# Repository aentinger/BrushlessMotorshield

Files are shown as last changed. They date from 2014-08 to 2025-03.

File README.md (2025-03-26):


💾 Brushless Motorshield
========================



# 📸 Image

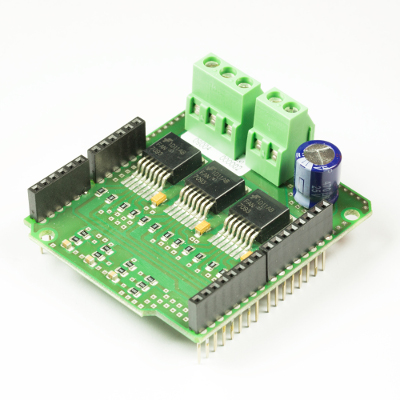
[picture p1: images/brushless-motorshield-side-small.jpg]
LXRobotics P3 BrushlessMotorshield


# 📂 Description

The Brushless Motorshield facilitates the control of a brushless motor with high performance (up to 46 A per phase). Furthermore so-called brushless gimbal motors can be controlled. For a quick and easy start, an open source Arduino library with sample programs is available.

**Features**

* Control of a brushless motor (BLDC Motor)
* Control of a Brushless Gimbal Motor
* Voltage supply range: 7.4 -14.8 V
* Can be used with 2S, 3S and 4S LiPo-battery
* High performance: Maximum continuous output current per phase: 46 A
* Motor drivers are protected against short circuit (to ground/supply), overheating, overvoltage and undervoltage
* Arduino Library with example programs is available on GitHub

# 🎥 [Video](images/brushless_motorshield_demo.mp4)

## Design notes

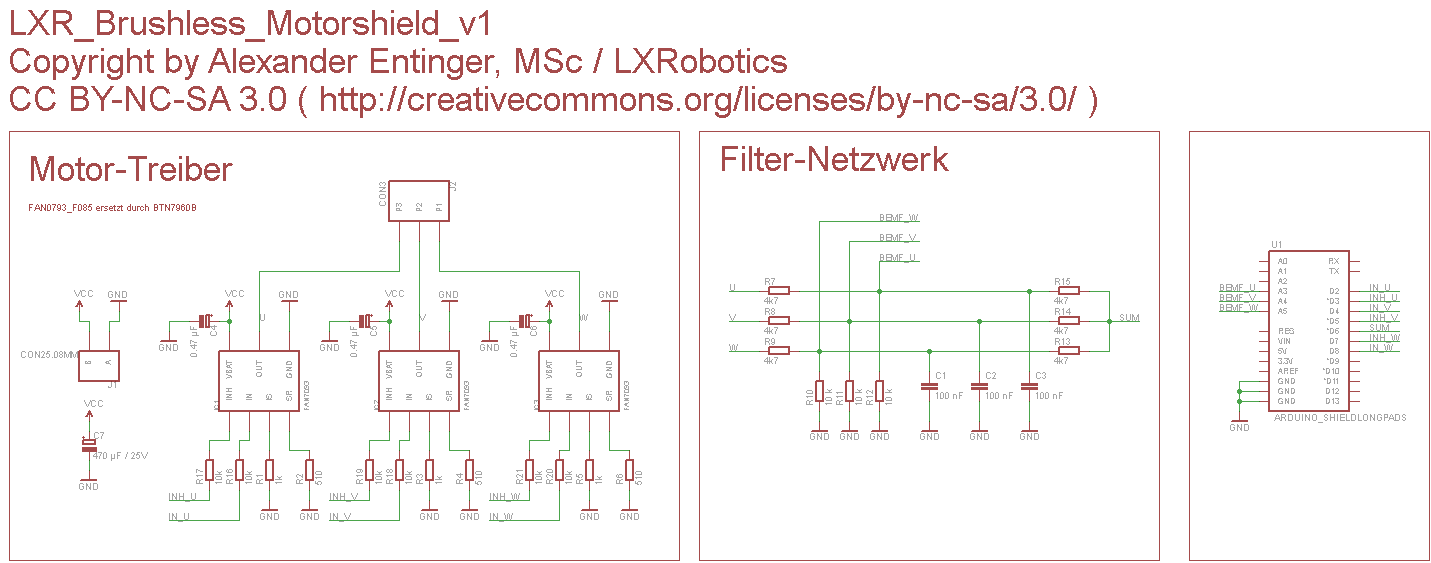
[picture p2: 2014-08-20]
hardware/lxr_brushless_motorshield_v1.png

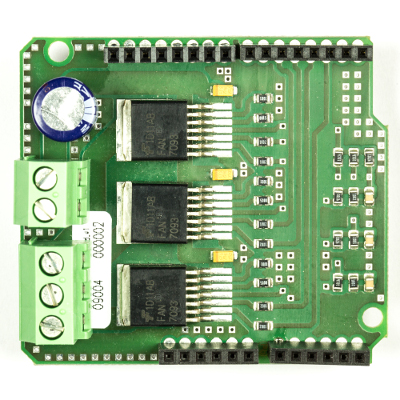
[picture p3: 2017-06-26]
images/brushless-motorshield-top-small.jpg

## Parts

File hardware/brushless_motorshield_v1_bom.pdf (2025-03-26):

Menge | Schaltplan | Bezeichnung | Farnell Bestell Nummer | Preis (1 Stück) | Gesamtpreis | Wird bestückt | Footprint | Säckchen | ESD
1 | J1 | Schraubklemme 2 Polig | 3041165 | € 1,12 | € 1,12 | | | S1
3 | IC1, IC2, IC3 | FAN7093 Leistungshalbbrücke | 2290282 | € | 6,99 | € | 20,97 | x | Bei Farnell aus dem Sortiment genommen, Ersatztyp ist BTN7960B, Digikey-Bauteil-Bezeichnung BTN7960BCT-ND
3 | C4, C5, C6 | KEMET Bauform A, 25 V, 470 nF, Tantal Ko | 1457425 | € 0,15 | € 0,46 | x
3 | C1, C2, C3 | 100 nF, 100 V, 0805, Keramikkondensator | 1759144 | € 0,01 | € 0,03 | x
1 | J2 | Schraubklemme 3 Polig | 3041177 | € 2,54 | € 2,54 | | S1
1 | C7 | 470 µF, 25 V, Elko, Radial | 1848502 | € 0,37 | € 0,37 | | S2 | x
9 | R10, R11, R12, R16, R17, R18, R19, R20, R21 | 10k, 0805, Widerstand SMD | 1469856 | € 0,02 | € 0,20 | x
3 | R1, R3, R5 | 1k, 0805, Widerstand SMD | 1469847 | € 0,02 | € 0,07 | x
3 | R2, R4, R6 | 510R, 0805, Widerstand SMD | 1653016 | € 0,10 | € 0,29 | x
6 | R7, R8, R9, R13, R14, R15 | 4k7, 0805, Widerstand SMD | 1469923 | € 0,02 | € 0,12 | x
1 | Satz Arduino Stiftleisten | ELV | € | 0,75 | € | 0,75 | - | http://www.elv.at/buchsenleisten-set-fuer-arduino-boards.html
| | | Summe | | € | 26,92

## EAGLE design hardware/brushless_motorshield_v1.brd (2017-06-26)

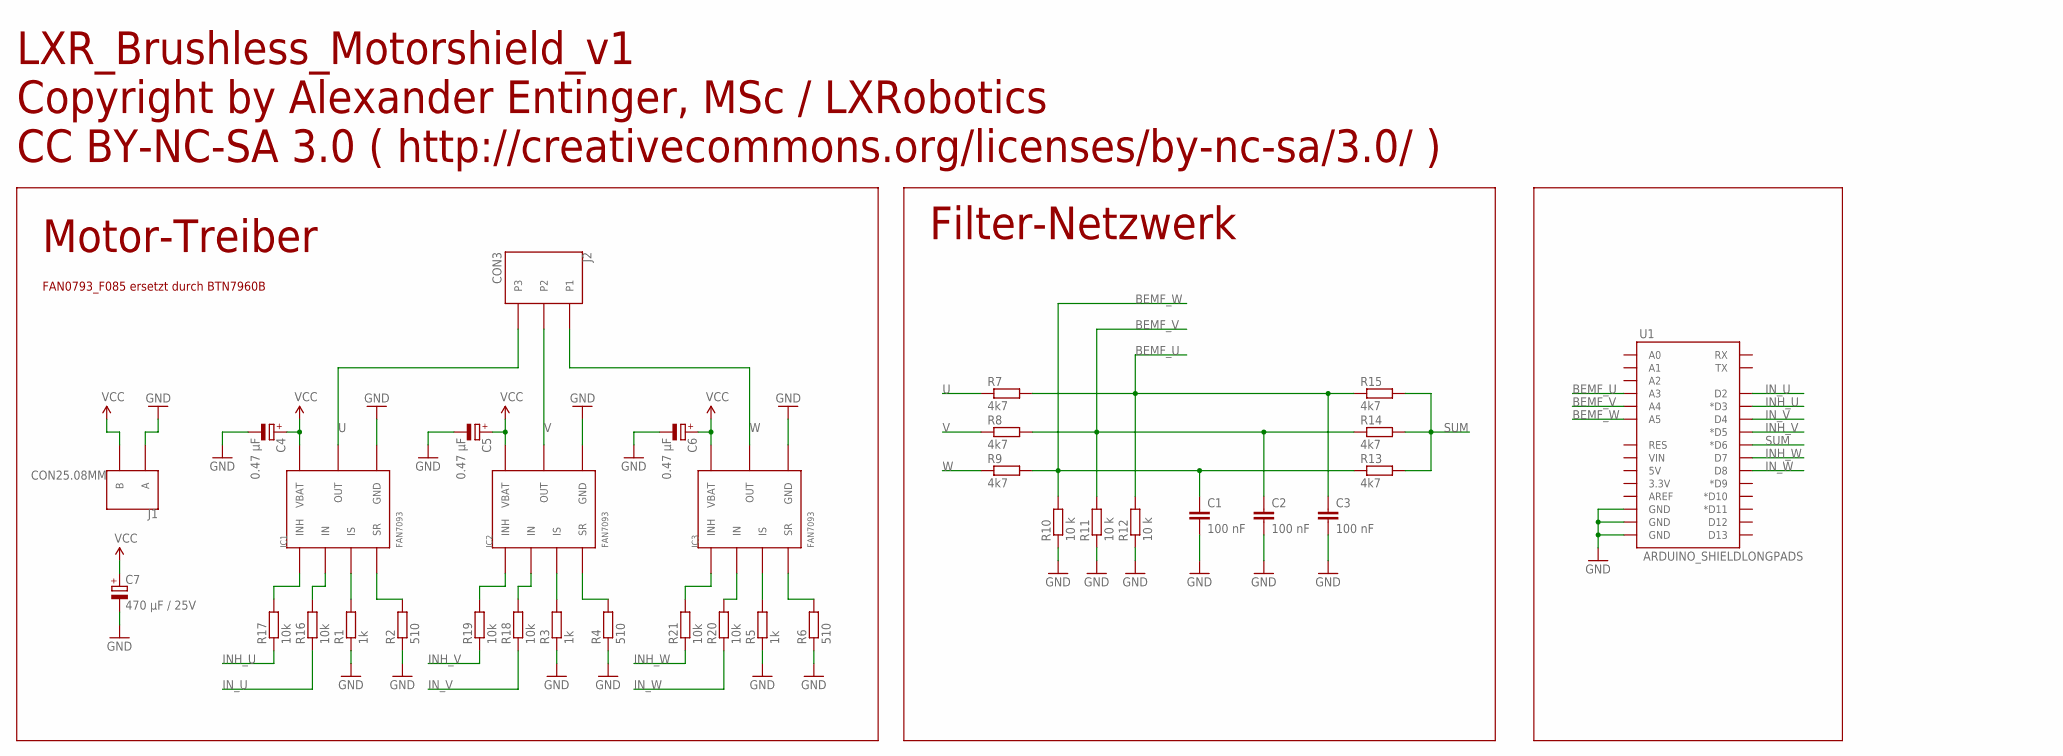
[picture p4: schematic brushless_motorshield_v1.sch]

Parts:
C1, C2, C3: 100 nF; C0805
C4, C5, C6: 0.47 µF; KEMET_A
C7: 470 µF / 25V; E5-10,5
IC1, IC2, IC3: FAN7093; TO263-7L
J1: CON25.08MM; CON2_SCHRAUBKLEMME
J2: CON3; CON3_SCHRAUBKLEMME
R1, R3, R5: 1k; R0805
R2, R4, R6: 510; R0805
R7, R8, R9, R13, R14, R15: 4k7; R0805
R10, R11, R12: 10 k; R0805
R16, R17, R18, R19, R20, R21: 10k; R0805
U1: ARDUINO_SHIELDLONGPADS; DUEMILANOVE_SHIELD_LONGPADS

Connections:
BEMF_U: C3.1, R7.2, R12.2, R15.1, U1.A3
BEMF_V: C2.1, R8.2, R11.2, R14.1, U1.A4
BEMF_W: C1.1, R9.2, R10.2, R13.1, U1.A5
GND: C1.2, C2.2, C3.2, C4.CATHODE (-), C5.CATHODE (-), C6.CATHODE (-), C7.-, IC1.GND, IC2.GND, IC3.GND, J1.1 (A), R1.1, R2.1, R3.1, R4.1, R5.1, R6.1, R10.1, R11.1, R12.1, U1.GND@0 (GND), U1.GND@1 (GND), U1.GND@2 (GND)
INH_U: R17.1, U1.D3 (*D3)
INH_V: R19.1, U1.D5 (*D5)
INH_W: R21.1, U1.D7
IN_U: R16.1, U1.D2
IN_V: R18.1, U1.D4
IN_W: R20.1, U1.D8
unnamed: IC1.IS, R1.2
unnamed: IC1.SR, R2.2
unnamed: IC2.IS, R3.2
unnamed: IC2.SR, R4.2
unnamed: IC3.IS, R5.2
unnamed: IC3.SR, R6.2
unnamed: IC1.INH, R17.2
unnamed: IC1.IN, R16.2
unnamed: IC3.INH, R21.2
unnamed: IC3.IN, R20.2
unnamed: IC2.INH, R19.2
unnamed: IC2.IN, R18.2
SUM: R13.2, R14.2, R15.2, U1.D6 (*D6)
U: IC1.OUT, IC1.OUT@1 (OUT), J2.P3, R7.1
V: IC2.OUT, IC2.OUT@1 (OUT), J2.P2, R8.1
VCC: C4.ANODE (+), C5.ANODE (+), C6.ANODE (+), C7.+, IC1.VBATT (VBAT), IC2.VBATT (VBAT), IC3.VBATT (VBAT), J1.2 (B)
W: IC3.OUT, IC3.OUT@1 (OUT), J2.P1, R9.1

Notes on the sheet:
LXR_Brushless_Motorshield_v1 Copyright by Alexander Entinger, MSc / LXRobotics CC BY-NC-SA 3.0 ( http://creativecommons.org/licenses/by-nc-sa/3.0/ )
Motor-Treiber
Filter-Netzwerk
FAN0793_F085 ersetzt durch BTN7960B

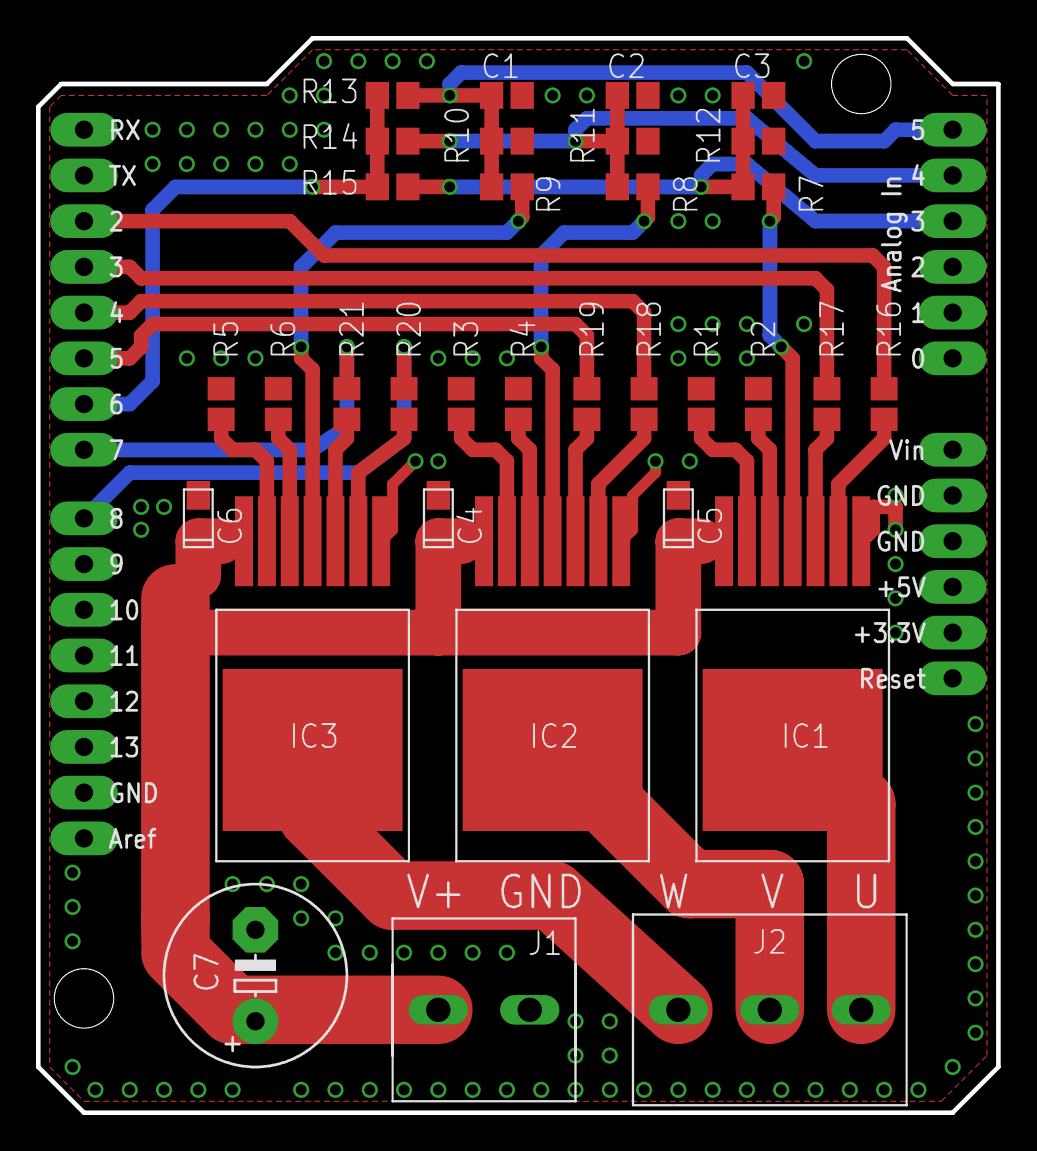
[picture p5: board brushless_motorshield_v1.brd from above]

Board: 2 copper layers, 53.3 x 59.7 mm, 34 parts (0 on the bottom side), 27 nets.

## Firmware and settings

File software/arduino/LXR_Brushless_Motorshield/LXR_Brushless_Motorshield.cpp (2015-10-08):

/**
 * @author Alexander Entinger, MSc / LXRobotics
 * @brief this file implements an arduino library to interface the LXRobotics Brushless Motorshield
 * @file LXR_Brushless_Motorshield.c
 * @license Attribution-NonCommercial-ShareAlike 3.0 Unported (CC BY-NC-SA 3.0) ( http://creativecommons.org/licenses/by-nc-sa/3.0/ )
 */

#include "LXR_Brushless_Motorshield.h"

/* C IMPLEMENTATION */

#include <avr/io.h>
#include <avr/interrupt.h>
#include <avr/wdt.h>
#include <util/delay.h>
#include <stdbool.h>

// enabling this defines puts the signal of the comparator isr on the digital pin D9 (PB1) ... useful for triggering the oszillocop
#define BRUSHLESS_DEBUG_OSZI

/* HARDWARE ABSTRACTION LAYER */
#ifdef BRUSHLESS_DEBUG_OSZI
// analog converter interrupt pin for triggering the oszi = D9 = PB1
#define AC_INT_DDR		(DDRB)
#define AC_INT_PORT		(PORTB)
#define AC_INT			(1<<1)
#endif
// IN_W = D8 = PB0
#define IN_W_DDR		(DDRB)
#define IN_W_PORT		(PORTB)
#define IN_W			(1<<0)
// INH_W = D7 = PD7
#define INH_W_DDR		(DDRD)
#define INH_W_PORT		(PORTD)
#define INH_W			(1<<7)
// IN_V = D4 = PD4
#define IN_V_DDR		(DDRD)
#define IN_V_PORT		(PORTD)
#define IN_V			(1<<4)
// INH_V = D5 = PD5
#define INH_V_DDR		(DDRD)
#define INH_V_PORT		(PORTD)
#define INH_V			(1<<5)
// IN_U = D2 = PD2
#define IN_U_DDR		(DDRD)
#define IN_U_PORT		(PORTD)
#define IN_U			(1<<2)
// INH_U = D3 = PD3
#define INH_U_DDR		(DDRD)
#define INH_U_PORT		(PORTD)
#define INH_U			(1<<3)
// MUX settings for connecting the bemf pin to the AIN1 input of the analog comparator
// BEMF_W = A5 = ADC5
#define MUX_BEMF_W_TO_AIN1	ADMUX &= 0xF0; ADMUX |= (1<<MUX2) | (1<<MUX0);
// BEMF_V = A4 = ADC4
#define MUX_BEMF_V_TO_AIN1	ADMUX &= 0xF0; ADMUX |= (1<<MUX2);
// BEMF_U = A3 = ADC3
#define MUX_BEMF_U_TO_AIN1	ADMUX &= 0xF0; ADMUX |= (1<<MUX1) | (1<<MUX0);

/* GLOBAL VARIABLES */
static volatile int8_t m_state = 0;
static volatile uint8_t m_speed = 0;
static volatile bool m_startup_complete = false;
static volatile E_DIRECTION m_dir = FORWARD;

/* PROTOTYPE SECTION */
void C_set_pins_according_to_state();

/* PROGRAM SECTION */

/**
 * @brief initializes the brushless motor control
 */
void C_init_brushless_motor_control() {
#ifdef BRUSHLESS_DEBUG_OSZI
  AC_INT_PORT &= ~AC_INT;
  AC_INT_DDR |= AC_INT;
#endif
  // set all IN_x ports to 0
  IN_U_PORT &= ~IN_U;
  IN_V_PORT &= ~IN_V;
  IN_W_PORT &= ~IN_W;
  // set all IN_x ports to outputs
  IN_U_DDR |= IN_U;
  IN_V_DDR |= IN_V;
  IN_W_DDR |= IN_W;
  // set all INH_X ports to 0
  INH_U_PORT &= ~INH_U;
  INH_V_PORT &= ~INH_V;
  INH_W_PORT &= ~INH_W;
  // set all INH_x ports to outputs
  INH_U_DDR |= INH_U;
  INH_V_DDR |= INH_V;
  INH_W_DDR |= INH_W;

  // set the pins according to the current state
  C_set_pins_according_to_state();

  // init the analog comparator
  // turn off adc
  ADCSRA &= ~(1<<ADEN);
  // turn off the digital input buffer on the pin AIN0 (PD6, SUM Signal)
  DIDR1 |= (1<<AIN0D);
  // turn off the digital input buffer on the pins ADC5, ADC4, ADC3
  DIDR0 |= (1<<ADC5D) | (1<<ADC4D) | (1<<ADC3D);
  // use multiplexer for negative comparator input
  ADCSRB |= (1<<ACME);
  // analog comparator is enabled
  ACSR &= ~(1<<ACD);
  // trigger interrupt on falling edge of comparator
  ACSR |= (1<<ACIS1);

  // init timer 2 (for pwm generation) - output is activated on timer overflow, deactivated at compare match
  // clear TCCR2A
  TCCR2A = 0x00;
  // clear TCNT2
  TCNT2 = 0;
  // enable timer 2 overflow and compare match a interrupt
  TIMSK2 |= (1<<TOIE2) | (1<<OCIE2A);
  // set compare match register to zero
  OCR2A = 0;
  // prescaler = 1, 1 Timerstep = 500 ns, 255 Timersteps = 127.5 usm, fPWM = 7,8 kHz
  TCCR2B = (1<<CS20);

  // init watchdog as timeout timer
  cli();
  wdt_reset();
  wdt_enable(WDTO_1S);
  WDTCSR |= (1<<WDCE) | (1<<WDIE) | (1<<WDP2) | (1<<WDP1); 
  sei();

}

/** 
 * @brief sets the speed for the brushless motor
 * @param speed
 */
void C_set_speed(uint8_t const speed) {
  m_speed = speed;
  OCR2A = m_speed;
  if(m_speed == 0) {
	TCCR2B &= ~(1<<CS20);
	ACSR &= ~(1<<ACIE);
        m_startup_complete = false;
        // set all IN_x ports to 0
        IN_U_PORT &= ~IN_U;
        IN_V_PORT &= ~IN_V;
        IN_W_PORT &= ~IN_W;
        // set all INH_X ports to 0
        INH_U_PORT &= ~INH_U;
        INH_V_PORT &= ~INH_V;
        INH_W_PORT &= ~INH_W;

	}
  else {
	 TCCR2B |= (1<<CS20);
	}	 
}
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

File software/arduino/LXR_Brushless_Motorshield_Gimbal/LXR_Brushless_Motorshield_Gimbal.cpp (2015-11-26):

/*
 * @author Alexander Entinger, MSc / LXRobotics
 * @brief this file implements the library to control a brushless gimbal motor with the LXRobotics Brushless Motorshield
 * @file LXR_Brushless_Motorshield_Gimbal.cpp
 * @license Attribution-NonCommercial-ShareAlike 3.0 Unported (CC BY-NC-SA 3.0) ( http://creativecommons.org/licenses/by-nc-sa/3.0/ )
 */ 

#include "LXR_Brushless_Motorshield_Gimbal.h"

#include <stdint.h>
#include <stdbool.h>
#include <avr/io.h>
#include <avr/interrupt.h>

/* DEFINES */
// IN_W = D8 = PB0
#define IN_W_DDR		(DDRB)
#define IN_W_PORT		(PORTB)
#define IN_W			(1<<0)
// INH_W = D7 = PD7
#define INH_W_DDR		(DDRD)
#define INH_W_PORT		(PORTD)
#define INH_W			(1<<7)
// IN_V = D4 = PD4
#define IN_V_DDR		(DDRD)
#define IN_V_PORT		(PORTD)
#define IN_V			(1<<4)
// INH_V = D5 = PD5
#define INH_V_DDR		(DDRD)
#define INH_V_PORT		(PORTD)
#define INH_V			(1<<5)
// IN_U = D2 = PD2
#define IN_U_DDR		(DDRD)
#define IN_U_PORT		(PORTD)
#define IN_U			(1<<2)
// INH_U = D3 = PD3
#define INH_U_DDR		(DDRD)
#define INH_U_PORT		(PORTD)
#define INH_U			(1<<3)

/* MACROS */
#define ENABLE_U() do { INH_U_PORT |= INH_U; } while (0)
#define ENABLE_V() do { INH_V_PORT |= INH_V; } while (0)
#define ENABLE_W() do { INH_W_PORT |= INH_W; } while (0)
#define SET_U_HIGH() do { IN_U_PORT |= IN_U; } while (0)
#define SET_V_HIGH() do { IN_V_PORT |= IN_V; } while (0)
#define SET_W_HIGH() do { IN_W_PORT |= IN_W; } while (0)
#define SET_U_LOW() do { IN_U_PORT &= ~IN_U; } while (0)
#define SET_V_LOW() do { IN_V_PORT &= ~IN_V; } while (0)
#define SET_W_LOW() do { IN_W_PORT &= ~IN_W; } while (0)

/* TYPEDEFS */
typedef enum {U = 0, V = 1, W = 2} E_PHASE_SELECT;
typedef struct 
{
	uint8_t ocr2a;
	E_PHASE_SELECT phase;
} s_phase_data;

typedef struct 
{
	s_phase_data phase_data[3];
	uint8_t phase_cnt;
} s_pwm_data;

/* GLOBAL VARIABLES */

static volatile E_DIRECTION m_direction = FORWARD;
static volatile uint8_t m_current_step_U = 0;
static volatile uint8_t m_current_step_V = 14;
static volatile uint8_t m_current_step_W = 28;
static volatile s_pwm_data m_pwm_data;

/* GLOBAL CONSTANTS */

static const uint8_t NUMBER_OF_STEPS = 42;
static const uint8_t SINUS[NUMBER_OF_STEPS] = {128,147,166,184,200,215,228,239,247,253,255,255,253,247,239,228,215,200,184,166,147,128,109,90,72,56,41,28,17,9,3,0,0,3,9,17,28,41,56,72,90,109};	

/* PROTOTYPES */

uint8_t increase_step(uint8_t const step);
void sort(s_phase_data *data, uint8_t const length);
void swap(s_phase_data *a, s_phase_data *b);

/* FUNCTIONS */

/** 
 * @brief initializes this library
 */	
void LXR_Brushless_Motorshield_Gimbal::begin() 
{
	  // set all IN_x ports to 0
	  IN_U_PORT &= ~IN_U;
	  IN_V_PORT &= ~IN_V;
	  IN_W_PORT &= ~IN_W;
	  // set all IN_x ports to outputs
	  IN_U_DDR |= IN_U;
	  IN_V_DDR |= IN_V;
	  IN_W_DDR |= IN_W;
	  // set all INH_X ports to 0
	  INH_U_PORT &= ~INH_U;
	  INH_V_PORT &= ~INH_V;
	  INH_W_PORT &= ~INH_W;
	  // set all INH_x ports to outputs
	  INH_U_DDR |= INH_U;
	  INH_V_DDR |= INH_V;
	  INH_W_DDR |= INH_W;
	  
	  // set up all params for the pwm generation my making one step
	  LXR_Brushless_Motorshield_Gimbal::step();
	 
	  // set up timer 2
	  TCCR2A = 0;
	  // reset timer
	  TCNT2 = 0;
	  // enable interrupts compare match A, timer overflow
	  TIMSK2 = (1<<OCIE2A) | (1<<TOIE2);
	  // run the timer
	  // prescaler = 8
	  // fTimer = fClk / 8 = 16 MHz / 8 = 2 MHz
	  // tTimerStep = 1 / 2 MHz = 500 ns
	  // tTimerCycle = 256 * tTimerStep = 128 us
	  // fTimerCycle = 1 / tTimerCycle = 7.8125 kHz
	  TCCR2B = (1<<CS21);
	  
	  // enable the bridges
	  ENABLE_U();
	  ENABLE_V();
	  ENABLE_W();
}
	
/**
 * @brief performs one step in the desired direction
 */
void LXR_Brushless_Motorshield_Gimbal::step() 
{
	// update step	
	m_current_step_U = increase_step(m_current_step_U);
	m_current_step_V = increase_step(m_current_step_V);
	m_current_step_W = increase_step(m_current_step_W);
	
	// setup phase data structs with the ocr values and phase
	s_phase_data phase_u, phase_v, phase_w;
	phase_u.ocr2a = SINUS[m_current_step_U];
	phase_u.phase = U;
	phase_v.ocr2a = SINUS[m_current_step_V];
	phase_v.phase = V;
	phase_w.ocr2a = SINUS[m_current_step_W];
	phase_w.phase = W;

	// create an array and sort it ascending
	s_phase_data phases[3] = {phase_u, phase_v, phase_w};
	sort(phases, 3);
	
	// update pwm data struct
	uint8_t p = 0; for(; p<3; p++) 
	{
		m_pwm_data.phase_data[p].ocr2a = phases[p].ocr2a;
		m_pwm_data.phase_data[p].phase = phases[p].phase;
	}
}
	
/**
 * @brief sets the direction for the brushless motor
 */
void LXR_Brushless_Motorshield_Gimbal::set_direction(E_DIRECTION const dir) 
{
	m_direction = dir;
}

/**
 * @brief increases by one step
 */
uint8_t increase_step(uint8_t const step) 
{
	if(step == (NUMBER_OF_STEPS - 1)) return 0;
	else return (step + 1);
}

/** 
 * @brief sorts the phases ascending by their ocr values
 */
void sort(s_phase_data *data, uint8_t const length) 
{
	bool elems_swapped = false;
	
	do 
	{
		elems_swapped = false;
		uint8_t i = 1; for(; i<length; i++) 
		{
			if(data[i-1].ocr2a > data[i].ocr2a) 
			{
				swap(&data[i-1], &data[i]);
				elems_swapped = true;
			}
		}
		
	} while(elems_swapped);
}

/** 
 * @brief swaps two structs
 */
void swap(s_phase_data *a, s_phase_data *b) 
{
	s_phase_data tmp = *a;
	*a = *b;
	*b = tmp;
}

/** 
 * @brief interrupt service routine for timer 2 overflow vector
 */
ISR(TIMER2_OVF_vect) 
{
	// turn on all phases
	if(SINUS[m_current_step_U] > 0) 
	{
	  if(m_direction == FORWARD) SET_U_HIGH();
    else SET_V_HIGH();
	}
	if(SINUS[m_current_step_V] > 0) 
	{
	  if(m_direction == FORWARD) SET_V_HIGH();
    else SET_U_HIGH();
	}
	if(SINUS[m_current_step_W] > 0) SET_W_HIGH();
	// update phase counter
	m_pwm_data.phase_cnt = 0;
	// update reg
	OCR2A = m_pwm_data.phase_data[m_pwm_data.phase_cnt].ocr2a;
}

/** 
 * @brief interrupt service routine for timer 2 compare match A vector
 */
ISR(TIMER2_COMPA_vect) 
{
	// turn off corresponding output
	switch(m_pwm_data.phase_data[m_pwm_data.phase_cnt].phase) 
	{
		case U: 
		{
		  if(m_direction == FORWARD) SET_U_LOW(); 
      else SET_V_LOW();
		}
    break;
		case V: 
		{
		  if(m_direction == FORWARD) SET_V_LOW(); 
      else SET_U_LOW();
		}
		break;
		case W: SET_W_LOW(); break;
		default: break;
	}
	// update phase counter
	m_pwm_data.phase_cnt++;
	// update register
	OCR2A = m_pwm_data.phase_data[m_pwm_data.phase_cnt].ocr2a;
}

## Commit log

2014-01-15 initial checkin for brushless motorshield
2014-04-25 adding direction control for brushless motorshield
2014-04-30 adding library for control of brushless gimbal motors
2015-10-08 bugfix by marco schilling (tu illmenau) - comparator interrupt is only enabled if speed is greater than zero - otherwise electrical noise can lead to an undesired positive feedback effect
    [LXR_Brushless_Motorshield.cpp, brushless_serial_control.ino]
2015-11-26 fixed small bug causing software not to work properly because TCCR2A is preset by arduino environment (init-function)
    [LXR_Brushless_Motorshield_Gimbal.cpp]
2017-06-26 Adding hardware files and images
    [brushless_motorshield_v1.brd, brushless_motorshield_v1.sch]
2025-03-26 Add BOM.

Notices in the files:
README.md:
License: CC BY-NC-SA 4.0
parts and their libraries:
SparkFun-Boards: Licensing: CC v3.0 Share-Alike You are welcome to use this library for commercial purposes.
